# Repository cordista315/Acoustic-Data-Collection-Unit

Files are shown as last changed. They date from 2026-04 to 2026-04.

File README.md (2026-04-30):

# BLE Acoustic Turntable — ECE 428

Bluetooth-controlled stepper motor turntable for rotating a ReSpeaker 6-Mic Circular Array at precise angular increments for acoustic localization research.

## Hardware

| Component | Part | Purpose |
|---|---|---|
| Microcontroller | ESP32 Dev Board | BLE communication + stepper control |
| Stepper driver | DRV8825 | Motor current control |
| Stepper motor | FLSUN 42SHDC40472-23B | Rotation (1.8°/step) |
| Microphone array | ReSpeaker 6-Mic Circular | Acoustic data capture |
| Power (motor) | 3S LiPo 11.1V 5200mAh | Motor supply |
| Power (logic) | USB power bank 5V | ESP32 supply |
| Capacitor | 100µF 35V electrolytic | VMOT spike suppression |
| Boost/buck | MT3608 or equivalent | Voltage regulation if needed |

## Wiring

```
ESP32 GPIO18  →  DRV8825 STEP
ESP32 GPIO19  →  DRV8825 DIR
ESP32 GPIO21  →  DRV8825 EN
ESP32 GPIO22  →  DRV8825 MODE0
ESP32 GPIO23  →  DRV8825 MODE1
ESP32 GPIO5   →  DRV8825 MODE2
ESP32 3.3V    →  DRV8825 VDD, RST, SLP
ESP32 GND     →  Shared GND rail
LiPo 11.1V    →  DRV8825 VMOT
GND           →  DRV8825 GND (motor side)
100µF cap     →  Across VMOT and GND (at DRV8825 pins)
DRV8825 1A/1B →  Motor Coil 1
DRV8825 2A/2B →  Motor Coil 2
```

Microstepping: MODE0=LOW, MODE1=HIGH, MODE2=LOW = 1/4 step
Resolution: 800 steps/rev = 0.45°/step

## Software Setup

### Requirements
- PlatformIO
- ESP32 board package
- ESP32 BLE Arduino library

### platformio.ini
```ini
[env:esp32dev]
platform  = espressif32
board     = esp32dev
framework = arduino
monitor_speed = 115200
lib_deps =
  ESP32 BLE Arduino
```

### Build and Flash
```bash
pio run -t upload
pio device monitor
```

## BLE Commands

Connect to device named **Turntable** using any Bluetooth-terminal for ios/android/pc

### Movement
| Command | Description |
|---|---|
| `STEP` | Advance one increment (default 2°) |
| `STEP:N` | Set increment to N° and advance |
| `BACK` | Reverse one increment |
| `BACK:N` | Reverse N degrees |
| `GOTO:N` | Move to absolute angle 0–360° |
| `RESET` | Return to 0° via shortest path |
| `ZERO` | Set current position as software 0° |

### Sweep / Scan
| Command | Description |
|---|---|
| `SWEEP` | Timer-based auto sweep 0→360° |
| `SCAN:N` | Synchronized scan in N° steps |
| `STOP` | Halt any active sweep or scan |
| `ACK` | Advance to next scan position (SCAN mode only) |

### Settings
| Command | Description |
|---|---|
| `SPEED:N` | Step delay in µs (100–10000, default 800) |
| `DWELL:N` | Sweep pause per position in ms (100–60000, default 1000) |
| `SETSTEP:N` | Set default increment without moving |
| `DIR:CW` | Force clockwise approach (reduces backlash) |
| `DIR:CCW` | Force counter-clockwise approach |
| `DIR:AUTO` | Shortest path (default) |
| `HOLD:ON` | Keep motor energized between moves (default) |
| `HOLD:OFF` | Disable motor between moves (runs cooler) |

### Info
| Command | Description |
|---|---|
| `STATUS` | Returns angle, step, speed, dwell, run, mode, dir, hold |
| `INFO` | Returns firmware version and motor config |

## SCAN Mode — Data Collection Flow

SCAN mode is the primary mode for acoustic data collection. The ESP32 and host stay synchronized — the motor never moves while the mic is recording.

```
Host  →  ESP32:  SCAN:2
ESP32 →  Host:   READY:0.00,TS:12345,STEP:2.00,RUN:1
[Host starts recording]
Host  →  ESP32:  ACK
ESP32 →  Host:   READY:2.00,TS:14201,STEP:2.00,RUN:1
[Host starts recording]
Host  →  ESP32:  ACK
... (180 positions for full 360° at 2° steps)
ESP32 →  Host:   SCAN_DONE,RUN:1
```

Each READY packet contains:
- Current angle in degrees
- Timestamp in milliseconds (millis() since boot)
- Step size
- Run number (auto-increments each SCAN or SWEEP)

## Additional Resources
- https://lastminuteengineers.com/drv8825-stepper-motor-driver-arduino-tutorial/
- https://www.monolithicpower.com/en/learning/resources/stepper-motors-basics-types-uses
- https://docs.espressif.com/projects/esp-idf/en/stable/esp32/api-guides/bt-architecture/overview.html
- https://docs.nordicsemi.com/bundle/ncs-latest/page/nrf/libraries/bluetooth/services/nus.html

## Advisor
Dr. Anthony Choi — Mercer University, Department of ECE

## Acknowledgements
This project was supported by NASA.

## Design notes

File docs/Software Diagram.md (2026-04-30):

```mermaid
flowchart TD
    %% =======================
    %% Initialization
    %% =======================
    Start([System Start])

    Setup["Initialize System<br/>• Configure GPIO<br/>• Set Microstepping (1/4)<br/>• Initialize BLE (GATT)<br/>• Start Advertising"]

    %% =======================
    %% Connection Handling
    %% =======================
    ConnCheck{"BLE Client<br/>Connected?"}
    Advertise["Continue Advertising"]

    %% =======================
    %% Main Loop
    %% =======================
    MainLoop["Main Control Loop"]

    ReadCmd["Read Incoming<br/>BLE Command"]

    CmdType{"Command Type"}

    %% =======================
    %% Actions
    %% =======================
    Rotate["Rotate Motor<br/>• Set Direction<br/>• Pulse STEP"]
    Stop["Stop Motor"]
    Idle["No Command / Idle"]

    %% Flow
    Start --> Setup --> ConnCheck

    ConnCheck -- No --> Advertise --> ConnCheck
    ConnCheck -- Yes --> MainLoop

    MainLoop --> ReadCmd --> CmdType

    CmdType -- "Rotate" --> Rotate --> MainLoop
    CmdType -- "Stop" --> Stop --> MainLoop
    CmdType -- "None" --> Idle --> MainLoop
```

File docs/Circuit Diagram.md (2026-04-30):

```mermaid
flowchart LR
    subgraph Power
        BATT["3S LiPo Battery<br/>11.1V 5200mAh"]
        CAP["100µF Capacitor (35V)<br/>Spike Suppression"]
    end

    subgraph Control
        ESP["ESP32<br/>BLE + Control Logic"]
    end

    subgraph Driver
        DRV["DRV8825 Stepper Driver"]
    end

    subgraph Actuator
        MOTOR["Stepper Motor"]
    end

    BATT -->|VMOT| CAP --> DRV
    ESP -->|3.3V Logic| DRV
    ESP -->|STEP| DRV
    ESP -->|DIR| DRV
    ESP -->|ENABLE| DRV
    DRV --> MOTOR

    GND["Common Ground"]
    SLP["SLEEP & RESET tied HIGH"]

    ESP --- GND
    DRV --- GND
    DRV --- SLP
```

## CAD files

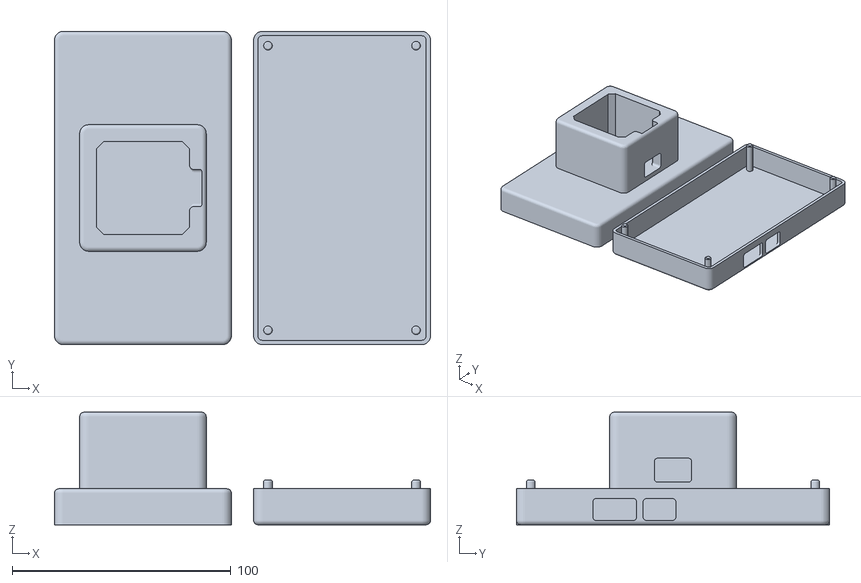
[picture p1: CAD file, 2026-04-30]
hardware/electronics enclosure.stl
172.0 x 143.3 x 51.5

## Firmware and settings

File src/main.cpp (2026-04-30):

/*
  BLE Turntable Controller — ReSpeaker Edition v2.3.0
  ESP32 + DRV8825 + FLSUN 42SHDC40472-23B (1.8deg/step)

  ── Wiring ────────────────────────────────────────
  GPIO18 → STEP
  GPIO19 → DIR
  GPIO21 → EN     (LOW = enabled)
  GPIO22 → MODE0
  GPIO23 → MODE1
  GPIO5  → MODE2
  RST    → 3.3V
  SLP    → 3.3V

  ── Microstepping ─────────────────────────────────
  MODE0=LOW MODE1=HIGH MODE2=LOW = 1/4 step
  200 full steps x 4 microsteps = 800 steps/rev
  Resolution = 360 / 800 = 0.45deg per microstep

  ── BLE Commands ──────────────────────────────────
  STEP / STEP:N / BACK / BACK:N / GOTO:N
  RESET / ZERO / SWEEP / SCAN:N / STOP
  SPEED:N / DWELL:N / SETSTEP:N
  DIR:CW / DIR:CCW / DIR:AUTO
  STATUS / INFO
*/

#include <Arduino.h>
#include <BLE2902.h>
#include <BLEDevice.h>
#include <BLEServer.h>
#include <BLEUtils.h>

#define FW_VERSION "2.3.0"

// ── Pins ───────────────────────────────────────────────────────────────────
#define PIN_STEP 18
#define PIN_DIR 19
#define PIN_EN 21
#define PIN_MS1 22
#define PIN_MS2 23
#define PIN_MS3 5

// ── Motor config ───────────────────────────────────────────────────────────
#define MICROSTEPS 4
#define FULL_STEPS_REV 200
#define MICROSTEPS_REV (FULL_STEPS_REV * MICROSTEPS)      // 800 steps/rev
#define DEGREES_PER_STEP (360.0f / (float)MICROSTEPS_REV) // 0.45 deg/step

// All angle tracking is in integer steps.
// TOTAL_STEPS = 800 = one full revolution.
// Target angles are converted to steps once and never back.

// ── BLE UUIDs ─────────────────────────────────────────────────────────────
#define SERVICE_UUID "6E400001-B5A3-F393-E0A9-E50E24DCCA9E"
#define CHAR_UUID_RX "6E400002-B5A3-F393-E0A9-E50E24DCCA9E"
#define CHAR_UUID_TX "6E400003-B5A3-F393-E0A9-E50E24DCCA9E"

// ── State ──────────────────────────────────────────────────────────────────
BLECharacteristic *pTxChar;
bool deviceConnected = false;

long currentSteps = 0; // absolute position in steps (wraps at MICROSTEPS_REV)
int stepDelayUs = 800;
int dwellMs = 1000;
int stepIncrSteps = 0; // stepIncrement stored as integer steps
float stepIncrDeg = 2.0f;
int runNumber = 0;
int approachDir = 0;     // 1=CW, -1=CCW, 0=auto
bool holdEnabled = true; // keep motor energized between moves

enum Mode { IDLE, SWEEPING, SCANNING };
Mode currentMode = IDLE;

bool scanWaitingForAck = false;
int scanStepSteps = 0; // scan step size in integer steps
float scanStepDeg = 2.0f;
unsigned long lastSweepTime = 0;

// ── Conversion helpers ────────────────────────────────────────────────────
// Always convert degrees→steps, never steps→degrees for logic
int degreesToSteps(float deg) { return (int)round(deg / DEGREES_PER_STEP); }

// Only for reporting to BLE — never used in motion logic
float currentAngleDeg() {
  long s = ((currentSteps % MICROSTEPS_REV) + MICROSTEPS_REV) % MICROSTEPS_REV;
  return s * DEGREES_PER_STEP;
}

// ── Motor control ──────────────────────────────────────────────────────────
void motorEnable() { digitalWrite(PIN_EN, LOW); }
void motorDisable() { digitalWrite(PIN_EN, HIGH); }

void stepMotor(int steps) {
  if (steps == 0) return;
  digitalWrite(PIN_DIR, steps > 0 ? HIGH : LOW);
  delayMicroseconds(2);
  int absSteps = abs(steps);
  for (int i = 0; i < absSteps; i++) {
    digitalWrite(PIN_STEP, HIGH);
    delayMicroseconds(stepDelayUs);
    digitalWrite(PIN_STEP, LOW);
    delayMicroseconds(stepDelayUs);
  }
  currentSteps += steps;
}

// ── Move by integer steps ─────────────────────────────────────────────────
void moveBySteps(int steps) {
  stepMotor(steps);
}

// ── Move to absolute target in integer steps ───────────────────────────────
// Everything is integer — no float conversion in logic path
void moveToSteps(int targetSteps) {
  // Normalize target into 0..MICROSTEPS_REV-1
  targetSteps = ((targetSteps % MICROSTEPS_REV) + MICROSTEPS_REV) % MICROSTEPS_REV;
  int current = (int)(((currentSteps % MICROSTEPS_REV) + MICROSTEPS_REV) % MICROSTEPS_REV);

  int delta = targetSteps - current;

  // Shortest path
  if (delta >  MICROSTEPS_REV / 2) delta -= MICROSTEPS_REV;
  if (delta < -MICROSTEPS_REV / 2) delta += MICROSTEPS_REV;

  // Integer deadband — if delta is 0 steps, do nothing at all
  if (delta == 0) return;

  // Approach direction override
  if (approachDir == 1 && delta < 0) {
    int overshoot = degreesToSteps(5.0f);
    stepMotor(delta - overshoot);
    stepMotor(overshoot);
  } else if (approachDir == -1 && delta > 0) {
    int overshoot = degreesToSteps(5.0f);
    stepMotor(delta + overshoot);
    stepMotor(-overshoot);
  } else {
    stepMotor(delta);
  }
}

void moveToAngle(float deg) {
  moveToSteps(degreesToSteps(deg));
}

void resetPosition() {
  moveToSteps(0);
  currentSteps = 0;
}

// ── BLE helpers ───────────────────────────────────────────────────────────
void sendBLE(String msg) {
  if (deviceConnected) {
    pTxChar->setValue(msg.c_str());
    pTxChar->notify();
  }
  Serial.println(">> " + msg);
}

String buildMeta(float stepDeg) {
  return "READY:" + String(currentAngleDeg(), 2) +
         ",TS:"   + String(millis()) +
         ",STEP:" + String(stepDeg, 2) +
         ",RUN:"  + String(runNumber);
}

void stopAll() {
  currentMode       = IDLE;
  scanWaitingForAck = false;
  motorDisable();
  sendBLE("STOPPED:" + String(currentAngleDeg(), 2));
}

// ── BLE server callbacks ───────────────────────────────────────────────────
class ServerCallbacks : public BLEServerCallbacks {
  void onConnect(BLEServer *pServer) {
    deviceConnected = true;
    sendBLE("READY,FW:v" + String(FW_VERSION));
  }
  void onDisconnect(BLEServer *pServer) {
    deviceConnected = false;
    currentMode = IDLE;
    scanWaitingForAck = false;
    motorDisable();
    pServer->startAdvertising();
  }
};

// ── Command parser ─────────────────────────────────────────────────────────
class RxCallbacks : public BLECharacteristicCallbacks {
  void onWrite(BLECharacteristic *pChar) {
    String cmd = String(pChar->getValue().c_str());
    cmd.trim();
    cmd.toUpperCase();
    Serial.println("<< " + cmd);

    // ── ACK ───────────────────────────────────────────────────────────────
    if (cmd == "ACK") {
      if (currentMode == SCANNING && scanWaitingForAck) {
        scanWaitingForAck = false;
        int current = (int)(((currentSteps % MICROSTEPS_REV) + MICROSTEPS_REV) % MICROSTEPS_REV);
        int next    = current + scanStepSteps;
        if (next >= MICROSTEPS_REV) {
          currentMode = IDLE;
          motorDisable();
          sendBLE("SCAN_DONE,RUN:" + String(runNumber));
        } else {
          motorEnable();
          moveToSteps(next);
          motorDisable();
          scanWaitingForAck = true;
          sendBLE(buildMeta(scanStepDeg));
        }
      } else {
        sendBLE("ERR:NO_SCAN_ACTIVE");
      }
      return;
    }

    // ── STOP ──────────────────────────────────────────────────────────────
    if (cmd == "STOP") { stopAll(); return; }

    // ── SCAN:N ────────────────────────────────────────────────────────────
    if (cmd.startsWith("SCAN:")) {
      float sz = cmd.substring(5).toFloat();
      if (sz <= 0 || sz > 180) { sendBLE("ERR:SCAN_STEP_RANGE_0.1-180"); return; }
      scanStepDeg   = sz;
      scanStepSteps = degreesToSteps(sz);
      currentMode   = SCANNING;
      scanWaitingForAck = false;
      runNumber++;
      motorEnable();
      moveToSteps(0);
      motorDisable();
      scanWaitingForAck = true;
      sendBLE(buildMeta(scanStepDeg));
      return;
    }

    // ── SWEEP ─────────────────────────────────────────────────────────────
    if (cmd == "SWEEP") {
      currentMode = SWEEPING;
      runNumber++;
      motorEnable();
      moveToSteps(0);
      lastSweepTime = millis();
      sendBLE("SWEEP_START,RUN:" + String(runNumber));
      return;
    }

    // ── RESET ─────────────────────────────────────────────────────────────
    if (cmd == "RESET") {
      currentMode = IDLE;
      scanWaitingForAck = false;
      motorEnable();
      resetPosition();
      motorDisable();
      sendBLE("ANGLE:0.00");
      return;
    }

    // ── ZERO ──────────────────────────────────────────────────────────────
    if (cmd == "ZERO") {
      currentSteps = 0;
      sendBLE("ZEROED");
      return;
    }

    // ── STATUS ────────────────────────────────────────────────────────────
    if (cmd == "STATUS") {
      sendBLE("ANGLE:"  + String(currentAngleDeg(), 2) +
              ",STEP:"  + String(stepIncrDeg, 2) +
              ",SPEED:" + String(stepDelayUs) +
              ",DWELL:" + String(dwellMs) +
              ",RUN:"   + String(runNumber) +
              ",MODE:"  + String(currentMode == IDLE ? "IDLE" : currentMode == SWEEPING ? "SWEEP" : "SCAN") +
              ",DIR:"   + String(approachDir == 0 ? "AUTO" : approachDir == 1 ? "CW" : "CCW") +
              ",HOLD:"  + String(holdEnabled ? "ON" : "OFF"));
      return;
    }

    // ── INFO ──────────────────────────────────────────────────────────────
    if (cmd == "INFO") {
      sendBLE("FW:"          + String(FW_VERSION) +
              ",MOTOR:42SHDC40472-23B" +
              ",STEPS_REV:"  + String(MICROSTEPS_REV) +
              ",DEG_STEP:"   + String(DEGREES_PER_STEP, 4) +
              ",MICROSTEPS:" + String(MICROSTEPS));
      return;
    }

    // ── HOLD ─────────────────────────────────────────────────────────────
    if (cmd == "HOLD:ON")  { holdEnabled = true;  motorEnable();  sendBLE("HOLD:ON");  return; }
    if (cmd == "HOLD:OFF") { holdEnabled = false; motorDisable(); sendBLE("HOLD:OFF"); return; }

    // ── DIR ───────────────────────────────────────────────────────────────
    if (cmd == "DIR:CW")   { approachDir =  1; sendBLE("DIR_SET:CW");   return; }
    if (cmd == "DIR:CCW")  { approachDir = -1; sendBLE("DIR_SET:CCW");  return; }
    if (cmd == "DIR:AUTO") { approachDir =  0; sendBLE("DIR_SET:AUTO"); return; }

    // ── Movement (IDLE only) ──────────────────────────────────────────────
    if (currentMode != IDLE) { sendBLE("ERR:BUSY,SEND_STOP_FIRST"); return; }

    motorEnable();

    if (cmd == "STEP") {
      moveBySteps(stepIncrSteps);
      sendBLE("ANGLE:" + String(currentAngleDeg(), 2));

    } else if (cmd == "BACK") {
      moveBySteps(-stepIncrSteps);
      sendBLE("ANGLE:" + String(currentAngleDeg(), 2));

    } else if (cmd.startsWith("STEP:")) {
      float deg = cmd.substring(5).toFloat();
      if (deg > 0 && deg <= 360) {
        stepIncrDeg   = deg;
        stepIncrSteps = degreesToSteps(deg);
        moveBySteps(stepIncrSteps);
        sendBLE("ANGLE:" + String(currentAngleDeg(), 2));
      } else sendBLE("ERR:INVALID_STEP");

    } else if (cmd.startsWith("BACK:")) {
      float deg = cmd.substring(5).toFloat();
      if (deg > 0 && deg <= 360) {
        moveBySteps(-degreesToSteps(deg));
        sendBLE("ANGLE:" + String(currentAngleDeg(), 2));
      } else sendBLE("ERR:INVALID_STEP");

    } else if (cmd.startsWith("GOTO:")) {
      float target = cmd.substring(5).toFloat();
      if (target >= 0 && target <= 360) {
        moveToAngle(target);
        sendBLE("ANGLE:" + String(currentAngleDeg(), 2));
      } else sendBLE("ERR:ANGLE_RANGE_0-360");

    } else if (cmd.startsWith("SETSTEP:")) {
      float deg = cmd.substring(8).toFloat();
      if (deg > 0 && deg <= 180) {
        stepIncrDeg   = deg;
        stepIncrSteps = degreesToSteps(deg);
        sendBLE("STEP_SET:" + String(stepIncrDeg, 2));
      } else sendBLE("ERR:SETSTEP_RANGE_0.1-180");

    } else if (cmd.startsWith("SPEED:")) {
      int spd = cmd.substring(6).toInt();
      if (spd >= 100 && spd <= 10000) { stepDelayUs = spd; sendBLE("SPEED_SET:" + String(stepDelayUs)); }
      else sendBLE("ERR:SPEED_RANGE_100-10000");

    } else if (cmd.startsWith("DWELL:")) {
      int dw = cmd.substring(6).toInt();
      if (dw >= 100 && dw <= 60000) { dwellMs = dw; sendBLE("DWELL_SET:" + String(dwellMs)); }
      else sendBLE("ERR:DWELL_RANGE_100-60000");

    } else {
      sendBLE("ERR:UNKNOWN_CMD");
    }
    // Respect hold setting after manual commands
    if (!holdEnabled) motorDisable();
    // Motor stays ENABLED after manual commands so it holds
    // its detent and doesn't jerk on re-energization.
    // It will be disabled after SWEEP/SCAN completes or on disconnect.
  }
};

// ── Setup ──────────────────────────────────────────────────────────────────
void setup() {
  Serial.begin(115200);

  pinMode(PIN_STEP, OUTPUT);
  pinMode(PIN_DIR,  OUTPUT);
  pinMode(PIN_EN,   OUTPUT);
  pinMode(PIN_MS1,  OUTPUT);
  pinMode(PIN_MS2,  OUTPUT);
  pinMode(PIN_MS3,  OUTPUT);

  // 1/4 step: MODE0=LOW MODE1=HIGH MODE2=LOW
  digitalWrite(PIN_MS1, LOW);
  digitalWrite(PIN_MS2, HIGH);
  digitalWrite(PIN_MS3, LOW);

  // Initialise step increment
  stepIncrSteps = degreesToSteps(stepIncrDeg);

  motorDisable();
  Serial.println("Turntable FW v" + String(FW_VERSION) +
                 " — 0.45deg/step, 800 steps/rev");

  BLEDevice::init("Turntable");
  BLEServer *pServer = BLEDevice::createServer();
  pServer->setCallbacks(new ServerCallbacks());
  BLEService *pService = pServer->createService(SERVICE_UUID);

  pTxChar = pService->createCharacteristic(
    CHAR_UUID_TX, BLECharacteristic::PROPERTY_NOTIFY);
  pTxChar->addDescriptor(new BLE2902());

  BLECharacteristic *pRxChar = pService->createCharacteristic(
    CHAR_UUID_RX,
    BLECharacteristic::PROPERTY_WRITE | BLECharacteristic::PROPERTY_WRITE_NR);
  pRxChar->setCallbacks(new RxCallbacks());

  pService->start();
  pServer->getAdvertising()->start();
  Serial.println("BLE advertising as 'Turntable'");
}

// ── Loop ───────────────────────────────────────────────────────────────────
void loop() {
  if (currentMode == SWEEPING) {
    unsigned long now = millis();
    if (now - lastSweepTime >= (unsigned long)dwellMs) {
      lastSweepTime = now;
      int current = (int)(((currentSteps % MICROSTEPS_REV) + MICROSTEPS_REV) % MICROSTEPS_REV);
      if (current + stepIncrSteps >= MICROSTEPS_REV) {
        currentMode = IDLE;
        motorDisable();
        sendBLE("SWEEP_DONE,RUN:" + String(runNumber));
      } else {
        motorEnable();
        moveBySteps(stepIncrSteps);
        motorDisable();
        sendBLE("ANGLE:" + String(currentAngleDeg(), 2) +
                ",TS:"   + String(millis()) +
                ",RUN:"  + String(runNumber));
      }
    }
  }
}

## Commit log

2026-04-30 Create Software flowchart.svg
2026-04-30 Create Circuit Diagram
2026-04-30 Update Circuit Diagram
2026-04-30 Rename Circuit Diagram to Circuit Diagram.md
2026-04-30 Update Software flowchart.svg
2026-04-30 Rename Software flowchart.svg to Software Flowchart.svg
2026-04-30 Rename Software Flowchart.svg to docs/Software Flowchart.svg
2026-04-30 Rename Circuit Diagram.md to docs/Circuit Diagram.md
2026-04-30 Create electronics enclosure
2026-04-30 Rename BoxV2.stl to electronics enclosure.stl
    [electronics enclosure.stl]
